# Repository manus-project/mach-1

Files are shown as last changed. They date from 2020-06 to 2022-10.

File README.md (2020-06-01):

# Manus MACH-1

This repository contains designs and assembly instructions for our first generation of manipulator.

 * [Bill of materials](bom.md) - list of materials used
 * [Frame parts](parts) - models of all 3D printer parts
 * [Pritned circuit boards](pcb) - schemes for PCB printing and assembly

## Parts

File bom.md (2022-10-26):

Bill or materials
=================

Manipulator
-----------

| Quantity | Name | Price per piece | Price | Manufacturer | Manufacturer’s code |
|---|---|---|---|---|---|
| 1 | HS-645MG Servo | 28.28 € | 28.28 € | HITEC | |
| 1 | HS-485HB Servo | 16.40 € | 16.40 € | HITEC | |
| 1 | HS-311 Servo | 8.94 € | 8.94 €  | HITEC | |
| 3 | ES08A Servo | 5.50 € | 16.50 € | EMAX | |
| 0.02 | Screw 2.2 mm 6.5 mm, Philips DIN 7982 | 13.08 € | 0.26 €  | TOOLCRAFT | 1068218 |
| 0.032 | Screw 2.2 mm 13 mm, Philips DIN 7982 | 15.54 € | 0.50 €  | TOOLCRAFT | 1068220 |
| 0.01 | PAN Screw TOOLCRAFT, M3, 25mm, DIN 7985 | 2.37 € | 0.02 €  | TOOLCRAFT | 827136 |
| 0.07 | PAN Screw TOOLCRAFT, M3, 20mm, DIN 7985 | 2.95 € | 0.21 €  | TOOLCRAFT | 815411 |
| 0.14 | M3 DIN 934,TOOLCRAFT 131823 | 0.82 € | 0.11 €  | TOOLCRAFT | 131823 |
| 0.24 | 3.2 mm DIN 433, TOOLCRAFT 106698 | 2.78 € | 0.67 €  | TOOLCRAFT | 106698 |
| 1 | SCI 6 A R13-112LP-02 LED GREEN250V/AC 6 A | 3.36 € | 3.36 €  | SCI | 700320 |
| 1 | 5.7 mm 2.1 mm BKL Electronic 072784 | 1.96 € | 1.96 €  | BKL | 72784 |
| 1.1 | Flat cable 10 X 0,14 AWG28 105°C | 0.42 € | 0.46 €  | Neltron | 830-127-10C |
| 1 | Audio cable 2x0,75 black-red | 0.43 € | 0.43 €  | Velleman | LOW2075RB/C |
| 1 | Axial bearing 51111 | 2.82 € | 2.82 €  | Codex | 51111 |

OpenServo board
---------------

| Quantity | PCB tag | Name | Description | Size | Price per piece | Price  | Manufacturer | Manufacturar’s code |
|---|---|---|---|---|---|---|---|---|
| 1 | IC1 | ATMEGA328P-AU |  8 Bit Microcontroller, Low Power High  Performance, ATmega, 20 MHz, 32 KB, 2 KB,  32 Pins, TQFP | TQFP | 3.20 € | 3.20 € | Microchip | ATMEGA328P-AU |
| 11 | C4, C5, C6, C7, C8, C9, C10, C11, C13, C16, C17 | MCB0603R104KCT | smd ceramic capacitor 0.1uF, 16V | V 0603 | 0.01 € | 0.09 € | Multicomp | MCB0603R104KCT |
| 2 | R8, R10 | MC0063W060312K | smd, resistro, 2k, 1% | V 0603 | 0.00 € | 0.01 € | Multicomp | MC0063W060312K |
| 1 | U2 | ZXCT1009F | current sensor, high side | V 0603 | 0.88 € | 0.88 € | Diodes inc. | ZXCT1009F |
| 1 | R2 | MC0063W060311K | smd resistor 1k 1%, 0603 | V 0603 | 0.01 € | 0.01 € | Multicomp | MC0063W060311K |
| 2 | R13, R15 | MC0063W06031100K | smd resistor, 100k 1% | V 0603 | 0.00 € | 0.00 € | Multicomp | MC0063W06031100K |
| 1 | R1 | MCCSM06FTDUR022 | smd current sense resistor, 0.022Ohm +-1% | V 1206 | 0.43 € | 0.43 € | Multicomp | MCCSM06FTDUR022 |
| 2 | U4, U5 | SN74CBT1G125DBVT | logic, switch bus fet sgl | SOT-23-5 | 0.32 € | 0.65 € | Texas Instruments | SN74CBT1G125DBVT |
| 2 | C3, C18 | C1608X7R1C105K080AC | smd ceramic capacitor 1uF, 16V +-10%, X7R | V 0603 | 0.06 € | 0.12 € | TDK | C1608X7R1C105K080AC |
| 4 | C1, C2, C14, C15 | C3216X7R1C106K160AC | smd ceramic capacitor 10uF, 16V +-10%, X7R | V 1206 | 0.30 € | 1.20 € | TDK | C3216X7R1C106K160AC |
| 1 | C12 | MCSH18B102K160CT | smd ceramic capacitor 1000pF, 16V +-10%, X7R | V 0603 | 0.04 € | 0.04 € | Multicomp | MCSH18B102K160CT |
| 1 | U3 | MCP9701AT-E/LT | temperature sensor IC | SC-70, 5pins | 0.39 € | 0.39 € | Microchip | MCP9701AT-E/LT |
| 1 | Q1 | CSTCE20M0V53 | resonator, ceramic, 20MHz, smd | | 0.43 € | 0.43 € | MURATA | CSTCE20M0V53-R0 |
| 1 | L1 | MLF1608E100K | inductor, high frequency, 10uH +-10 | V 0603 | 0.21 € | 0.21 € | TDK | MLF1608E100K |
| 2 | Q2, Q3 | IRF7317PBF | dual MOSFET, N and P channel, 6.6A, 20V | SOIC | 0.84 € | 1.67 € | INFINEON | IRF7317PBF |
| 2 | Q4, Q5 | NX7002BK | N Channel, 270 mA, 60 V, 2.2 ohm, 10 V, 1.6 V | SOT-23 | 0.04 € | 0.08 € | NEXPERIA | NX7002BKR |
| 7 | R4. R5, R7, R16, R17, R18, R19 | MC0063W0603110K | 10k 1% | V 0603 | 0.00 € | 0.03 € | Multicomp | MC0063W0603110K |
| 4 | R9, R11, R12, R14 | MC0063W0603110R | 10 R 1% | V 0603 | 0.00 € | 0.01 € | Multicomp | MC0063W0603110R |
| 1 | R3 | MC0063W060317K5 | 7.5k 1% | V 0603 | 0.00 € | 0.00 € | Multicomp | MC0063W060317K5 |
| 0.125 | | Header, male | 2x40 | | 0.34 € | 0.04 € | Neltron | 2213S-80G |
| 1 | | Connector | conector speedy 6 fimale | | 0.27 € | 0.27 € | Amphenol | T812106A101CEU |
| 1 | | PCB | | | 2.10 € | 2.10 € | | |

Raspberry Pi Shield
-------------------

| Quantity | PCB tag | Name | Price per piece | Price  | Manufacturer | manufacturer’s code |
|---|---|---|---|---|---|---|
| 1 | D1 | LITTELFUSE  SMBJ5.0A  TVS Diode, Transil SMBJ Series, Unidirectional, 5 V, 9.2 V, DO-214AA, 2 Pins | 0.32 € | 0.32 € | LITTELFUSE | SMBJ5.0A |
| 1 | IC1 | ON SEMICONDUCTOR  PCA9306DTR2G  Voltage Level Translator, Bidirectional, 2 Input, 64 mA, 1.5 ns, 0 V to 5.5 V, TSSOP-8 | 0.72 € | 0.72 € | ON SEMICONDUCTOR | PCA9306DTR2G |
| 1 | U1 | TEXAS INSTRUMENTS  LM4670SD  Audio Power Amplifier, D, 1 Channel, 3 W, 2.4V to 5.5V, LLP, 8 Pins | 1.02 € | 1.02 € | TEXAS INSTRUMENTS | LM4670SD |
| 2 | C2, C9 | PANASONIC ELECTRONIC COMPONENTS  EEEFPJ470UAR  SMD Aluminium Electrolytic Capacitor, Radial Can - SMD, 47 µF, 6.3 V, 0.85 ohm, FP Series | 0.32 € | 0.64 € | PANASONIC ELECTRONIC COMPONENTS | EEEFPJ470UAR |
| 6 | C3, C4, C5, C6, C8, C11 | KEMET  C0805C104K4RACTU  SMD Multilayer Ceramic Capacitor, 0805 [2012 Metric], 0.1 µF, 16 V, ± 10%, X7R, C Series | 0.06 € | 0.37 € | KEMET | C0805C104K4RACTU |
| 3 | C1, C7, C10 | KEMET  C0805C105K4RACTU  SMD Multilayer Ceramic Capacitor, 0805 [2012 Metric], 1 µF, 16 V, ± 10%, X7R, C Series | 0.07 € | 0.20 € | KEMET | C0805C105K4RACTU |
| 1 | U$1 | BOURNS  MF-MSMF150-2  PPTC Resettable Fuse, SMD, MF-MSMF Series, 1.5 A, 3 A, 6 V, -40 °C | 0.32 € | 0.32 € | BOURNS | MF-MSMF150-2 |
| 1 | | PRO SIGNAL  ABS-215-RC  Speaker, Mini, Mylar Cone, 1.5 W, 8 ohm, 550 Hz to 4500 Hz | 2.07 € | 2.07 € | PRO SIGNAL | ABS-215-RC |
| 1 | Q1 | VISHAY  SI4477DY-T1-GE3  MOSFET Transistor, P Channel, -26.6 A, -20 V, 0.0051 ohm, -4.5 V, -1.5 V | 1.30 € | 1.30 € | VISHAY | SI4477DY-T1-GE3 |
| 1 | Q2 | FAIRCHILD SEMICONDUCTOR  2N7002  MOSFET Transistor, N Channel, 115 mA, 60 V, 1.2 ohm, 10 V, 2.1 V | 0.19 € | 0.19 € | FAIRCHILD SEMICONDUCTOR |  2N7002 |
| 1 | IC2 | ON SEMICONDUCTOR  MC14027BDG  Flip-Flop, Master/Slave,Complementary Output, Positive Edge, MC14027, JK, 150 ns, 13 MHz, 8.8 mA | 0.42 € | 0.42 € | ON SEMICONDUCTOR | MC14027BDG |
| 1 | SV1 | LETVICA 2x6 Ž PROF. VISOKA R=2,54 | 0.46 € | 0.46 € | Neltron | 6803S-12-80 |
| 4 | 5V, SPEAKER, P_M, M | VRSTNA SPONKA ZA TIV 90° 2P - NIZKA (ZELENA) | 0.35 € | 1.40 € | TE Connectivity | 0-0282836-2 |
| 2 | R12, R15 | Resistor 10R 0603 1% SMD | 0.03 € | 0.05 € | Vishay | CRCW060310R0FKTABC  |
| 2 | R3, R4 | Resistor 340R 0603 1% SMD | 0.03 € | 0.05 € | Yageo | RC0603FR-07340RL |
| 3 | R17, R18, R19 | Resistor 511R 0603 1% SMD | 0.03 € | 0.08 € | Yageo | RC0603FR-07511RL |
| 3 | R16 | Resistor 1K 0603 1% SMD | 0.03 € | 0.08 € | Vishay | CRCW06031K00FKTABC  |
| 1 | R21 | Resistor 2K 0603 1% SMD 7" | 0.03 € | 0.03 € | Vishay | CRCW06032K00FKTABC  |
| 3 | R13, R14, R20 | Resistor 10K 0603 1% SMD | 0.03 € | 0.08 € | Vishay | CRCW060310K0FKTABC  |
| 6 | R5, R6, R7, R8, R9, R10 | Resistor 150K 0603 1% SMD | 0.03 € | 0.15 € | Vishay | CRCW0603150KFKTABC  |
| 0.125 | SV2 | Header2X40 M R=2,54 | 0.34 € | 0.04 € | Neltron | 2213S-80G |
| 1 | | PCB | 4.38 € | 4.38 € | | |

Other
-----

| Quantity | Name | Price per piece | Price | Manufacturer | Manufacturer’s code |
|---|---|---|---|---|---|
| 1 | RASPBERRYPI3-MODB-1GB | 32.79 € | 32.79 € | RASPBERRY-PI | RASPBERRYPI3-MODB-1GB |
| 1 | SanDisk SDHC 16GB Ultra UHS-I 80MB/s | 7.41 € | 7.41 €  | SanDisk | |
| 1 | Mean Well SGA60E05-P1J 5 V/DC 6000 mA 30 W | 30.29 € | 30.29 € | Mean Well | SGA60E05-P1J |
| 0.3 | Filament PrimaValue PLA 1kg | 22.13 € | 6.64 €  | PRIMA | |

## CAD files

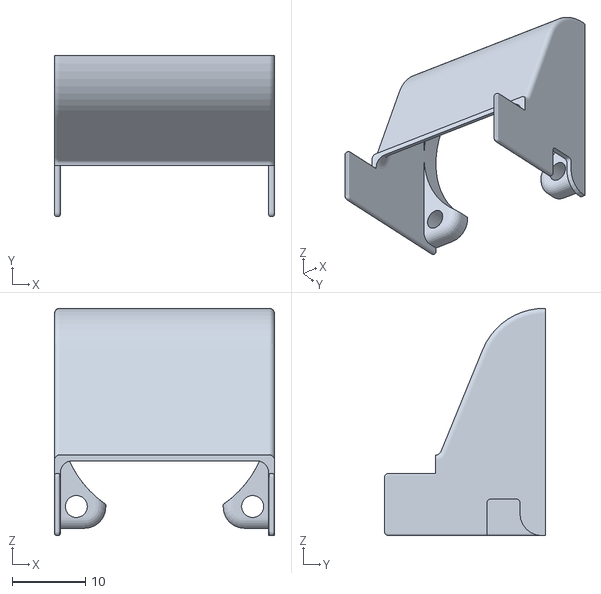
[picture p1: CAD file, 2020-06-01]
parts/base/cooling_tunnel.obj
30.0 x 22.0 x 31.0

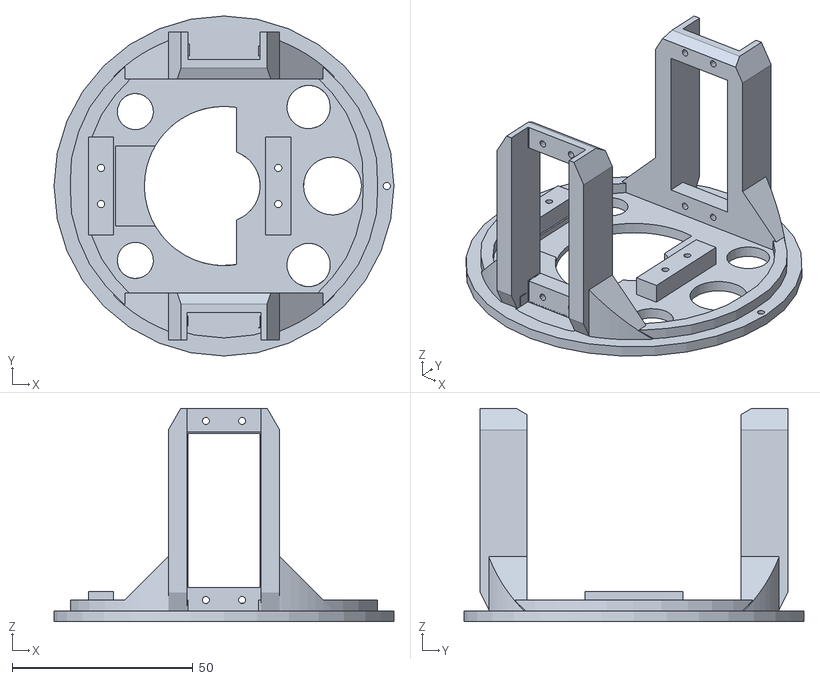
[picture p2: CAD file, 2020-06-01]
parts/manipulator/base_A.obj
94.0 x 94.0 x 59.0

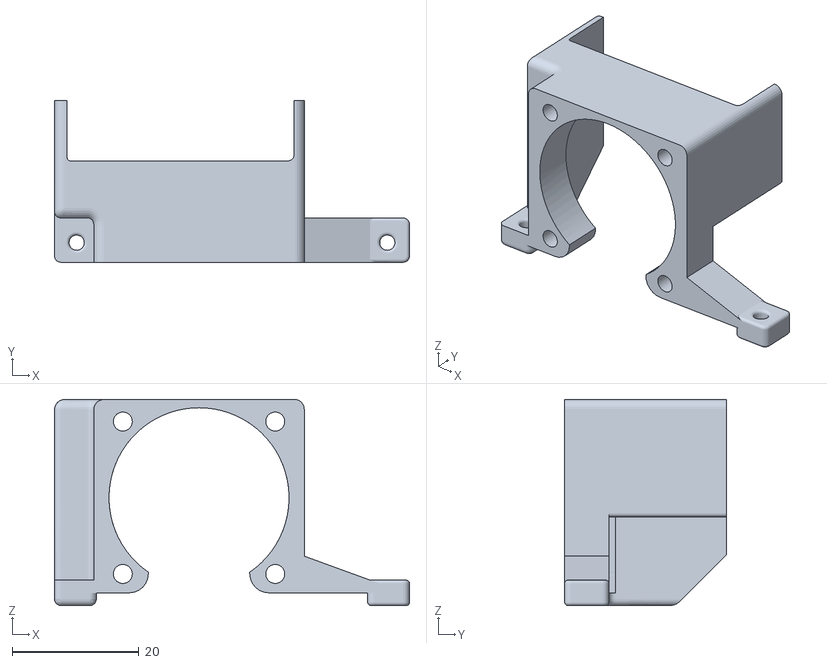
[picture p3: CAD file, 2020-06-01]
parts/base/cooling_fan.obj
56.0 x 25.5 x 32.5

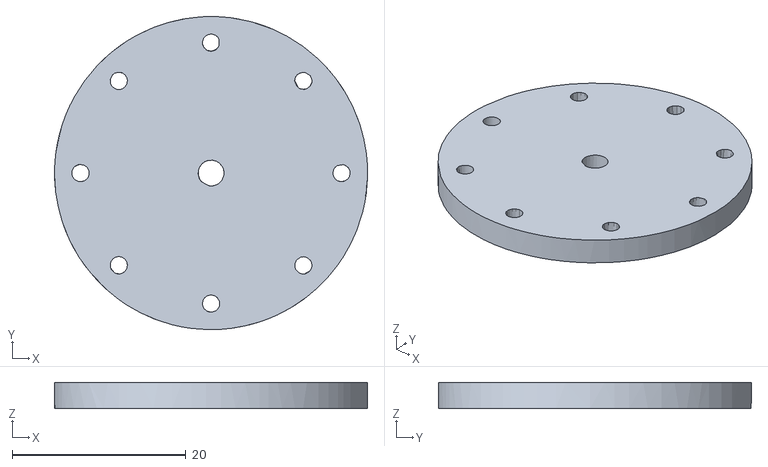
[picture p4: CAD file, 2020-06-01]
parts/manipulator/base_O.obj
36.0 x 36.0 x 3.00

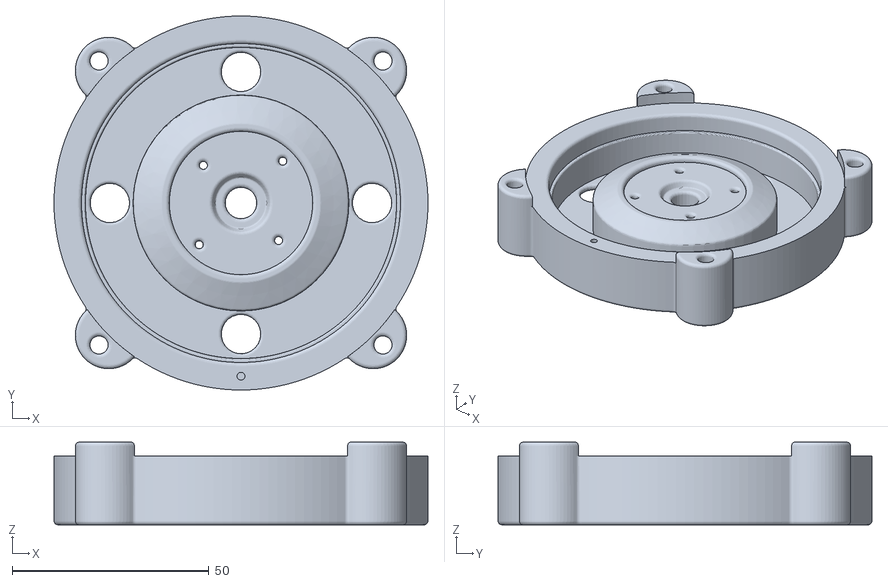
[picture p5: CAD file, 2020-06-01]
parts/base/base.obj
95.0 x 95.0 x 21.0

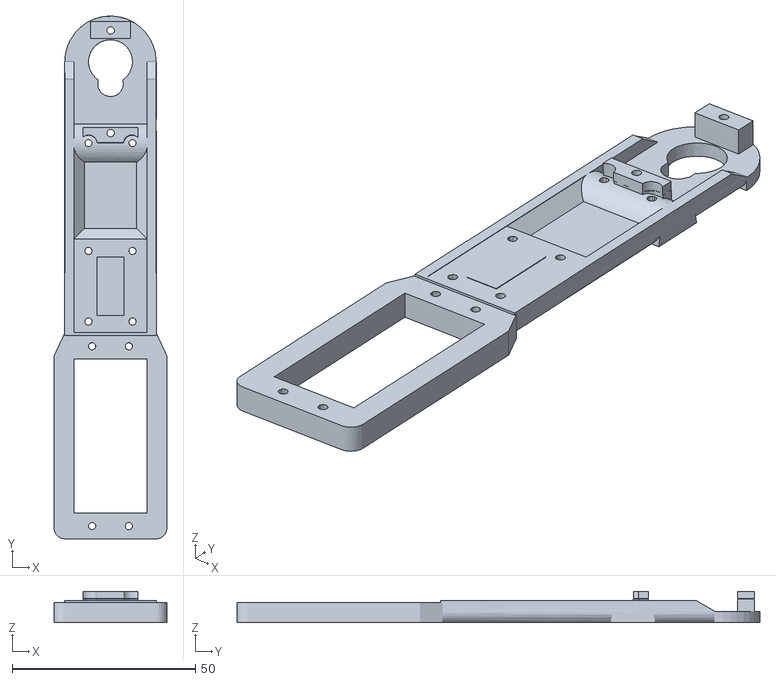
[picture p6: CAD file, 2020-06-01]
parts/manipulator/joint2_I_p1.obj
30.8 x 142.5 x 8.50

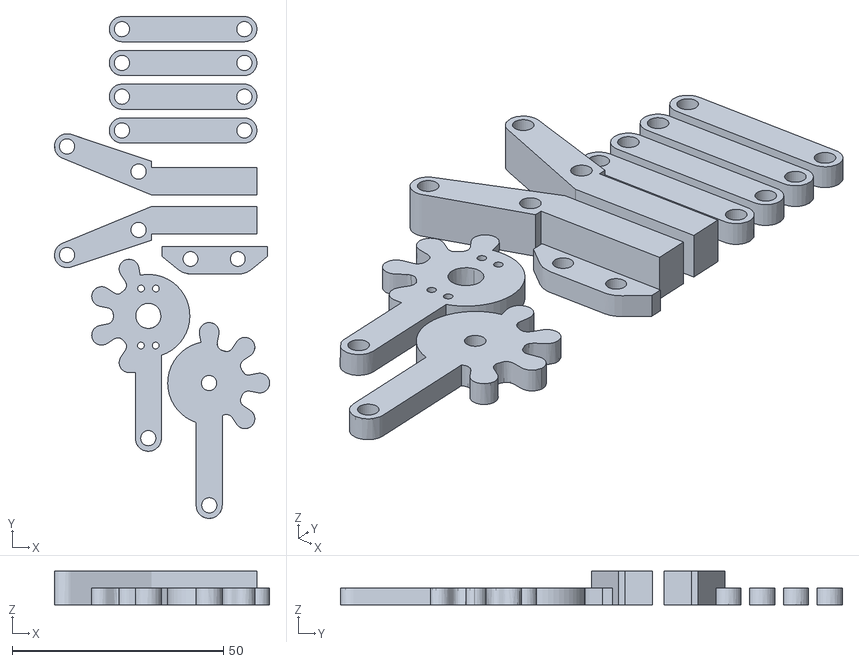
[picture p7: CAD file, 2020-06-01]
parts/manipulator/gripper.obj
51.0 x 118.9 x 8.00

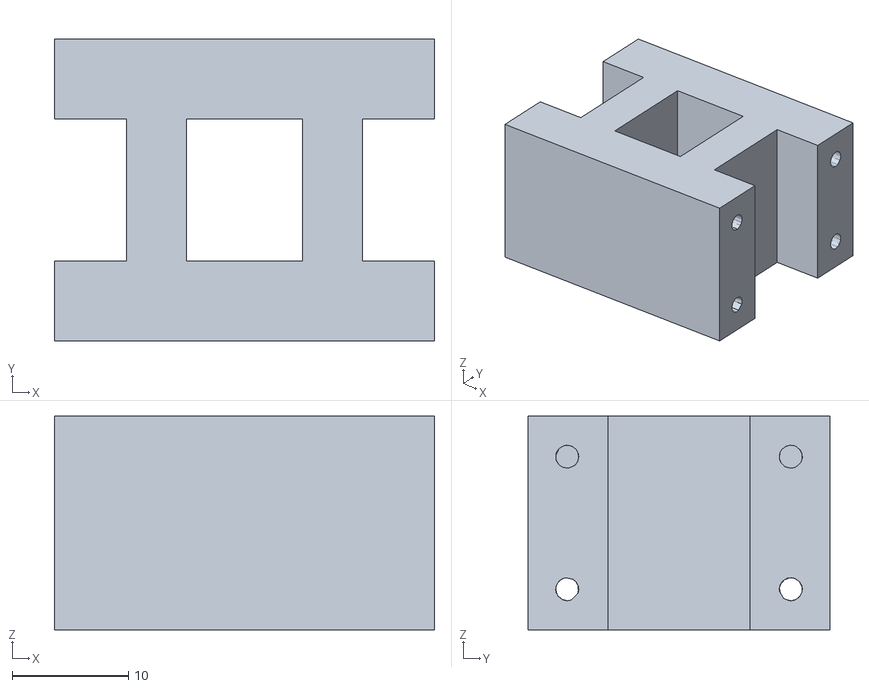
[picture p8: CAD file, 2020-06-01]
parts/manipulator/joint2_H.obj
32.7 x 26.0 x 18.4

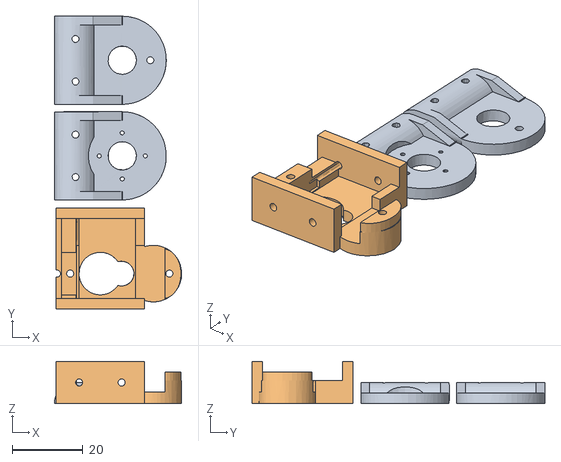
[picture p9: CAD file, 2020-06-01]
parts/manipulator/joint3.obj
36.0 x 82.7 x 12.0

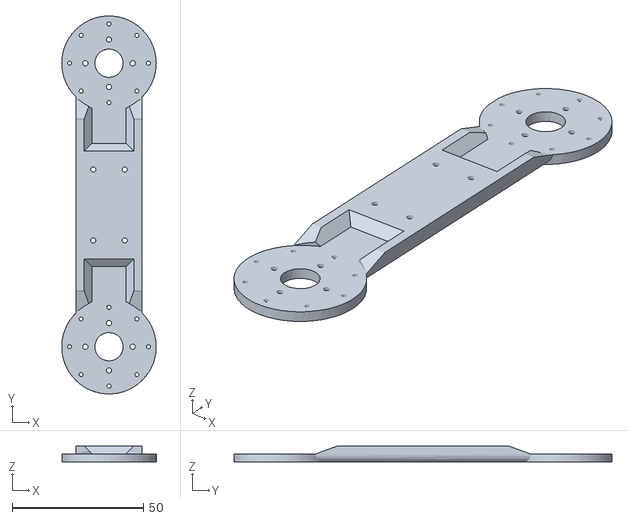
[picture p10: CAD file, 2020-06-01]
parts/manipulator/joint1_I.obj
36.0 x 144.0 x 6.00

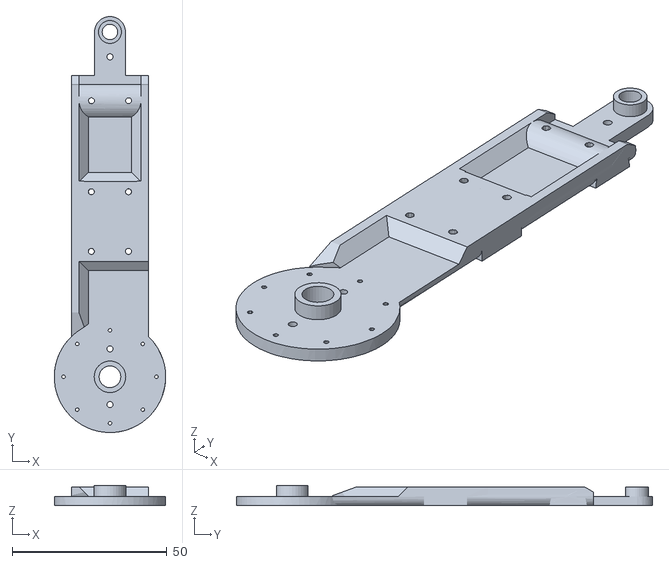
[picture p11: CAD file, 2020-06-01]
parts/manipulator/joint2_I_p2.obj
36.0 x 134.3 x 6.50

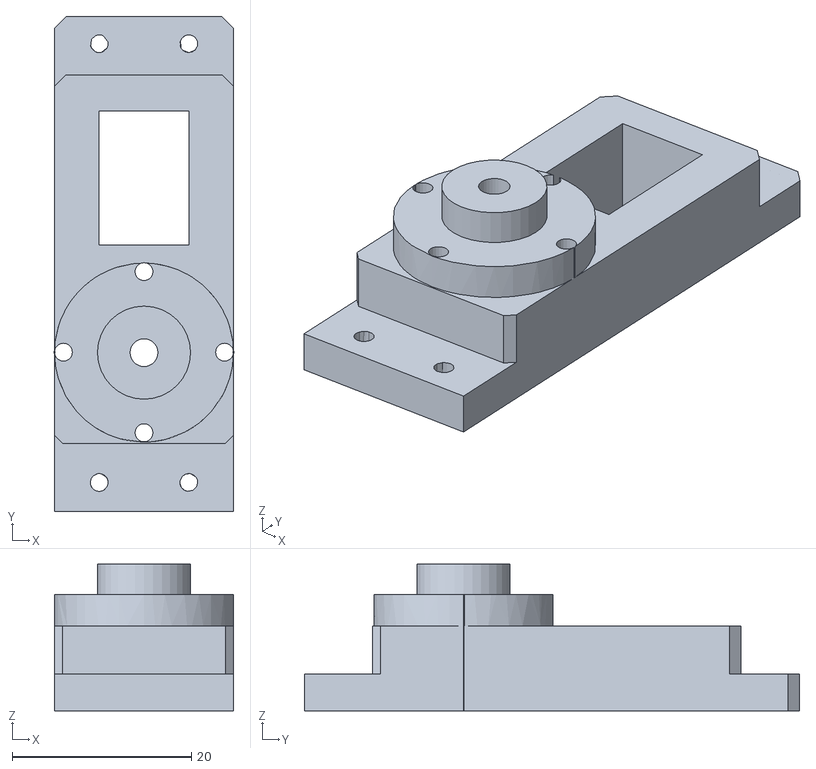
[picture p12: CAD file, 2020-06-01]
parts/manipulator/base_Servo.obj
20.0 x 55.3 x 16.4

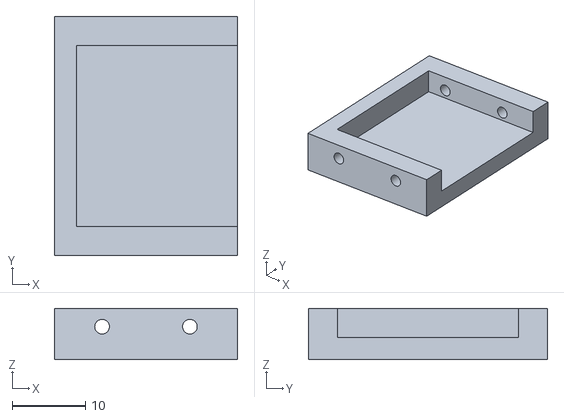
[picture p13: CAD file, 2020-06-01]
parts/manipulator/joint2_L.obj
25.0 x 32.7 x 7.00

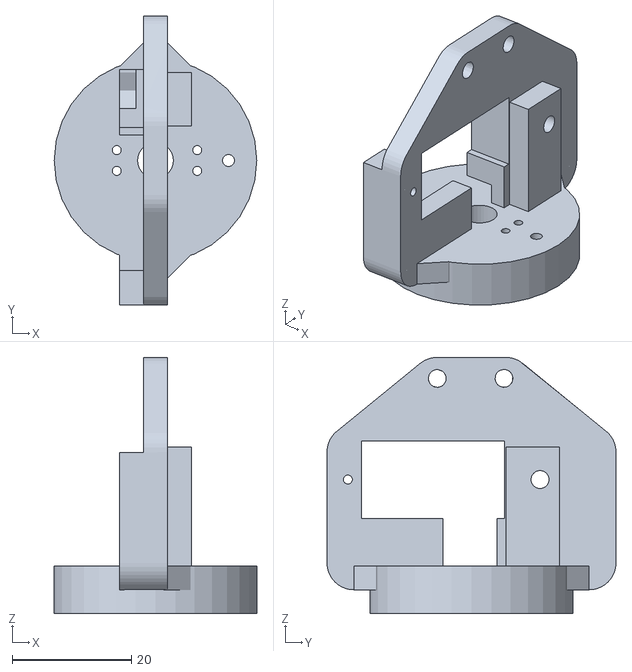
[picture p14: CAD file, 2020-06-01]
parts/manipulator/joint4.obj
34.0 x 48.5 x 43.0

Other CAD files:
parts/manipulator/joint1_H.obj

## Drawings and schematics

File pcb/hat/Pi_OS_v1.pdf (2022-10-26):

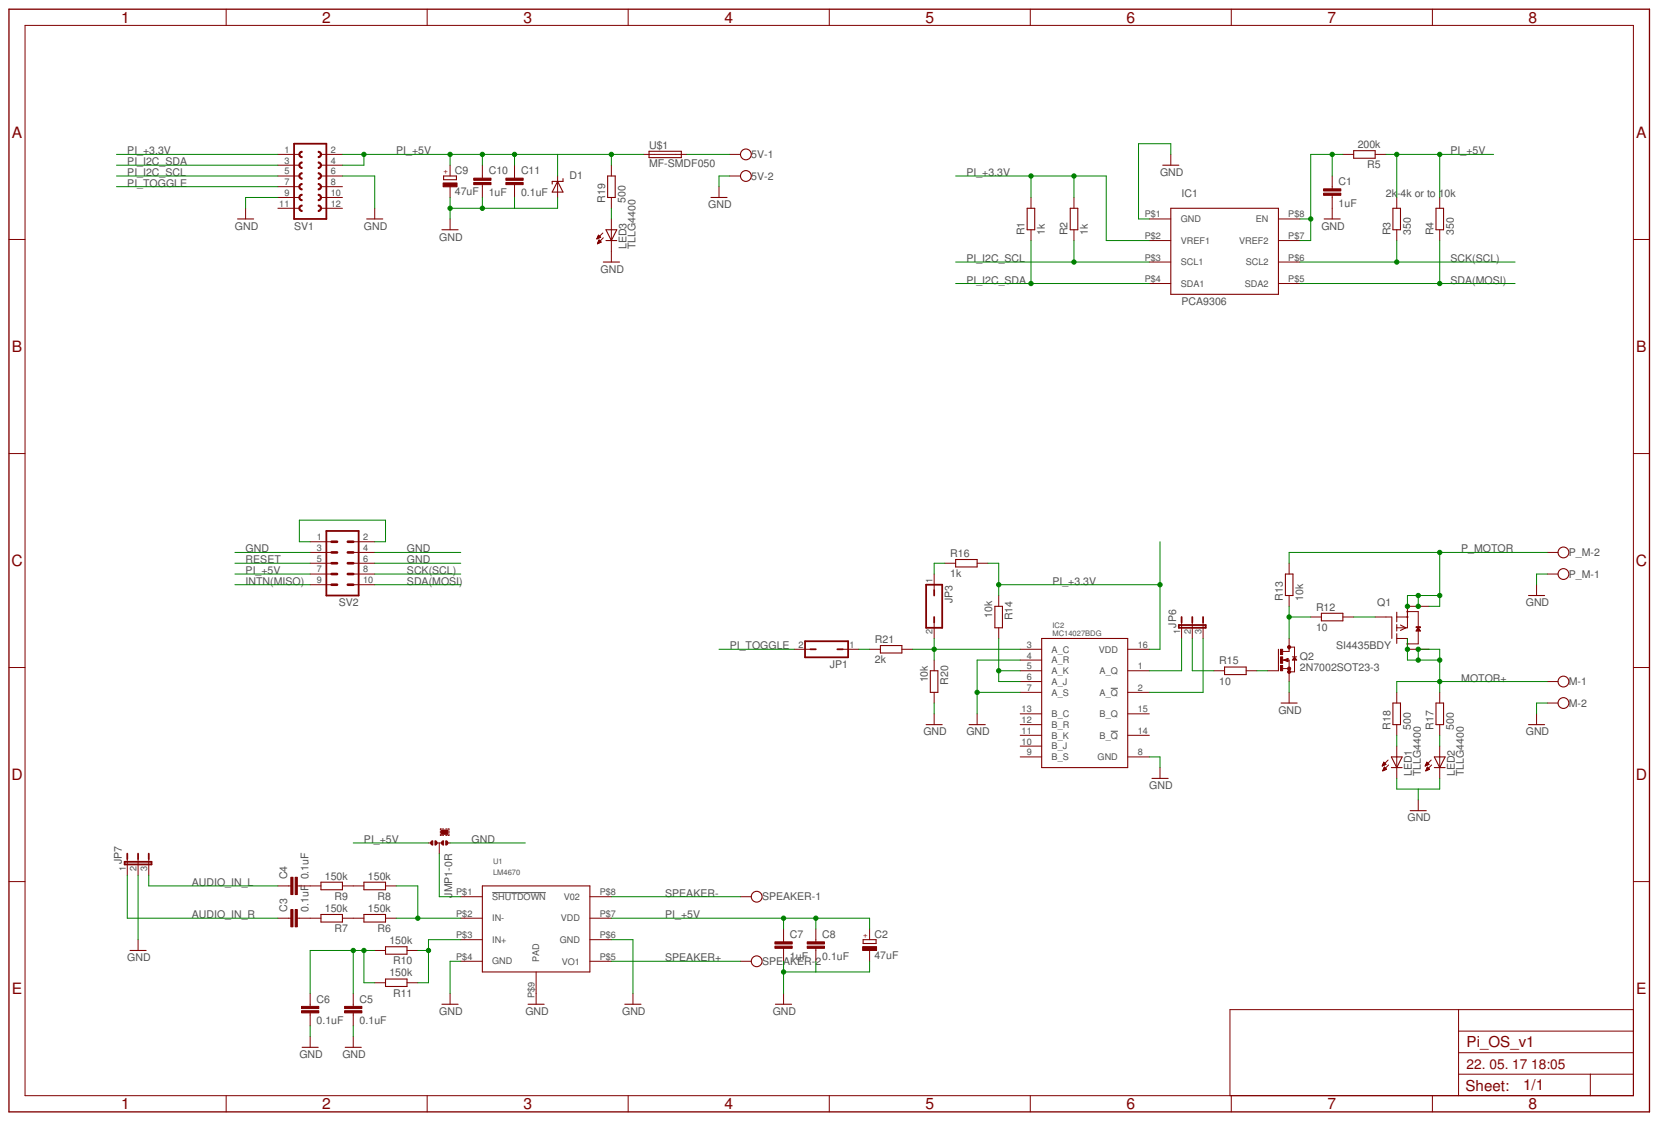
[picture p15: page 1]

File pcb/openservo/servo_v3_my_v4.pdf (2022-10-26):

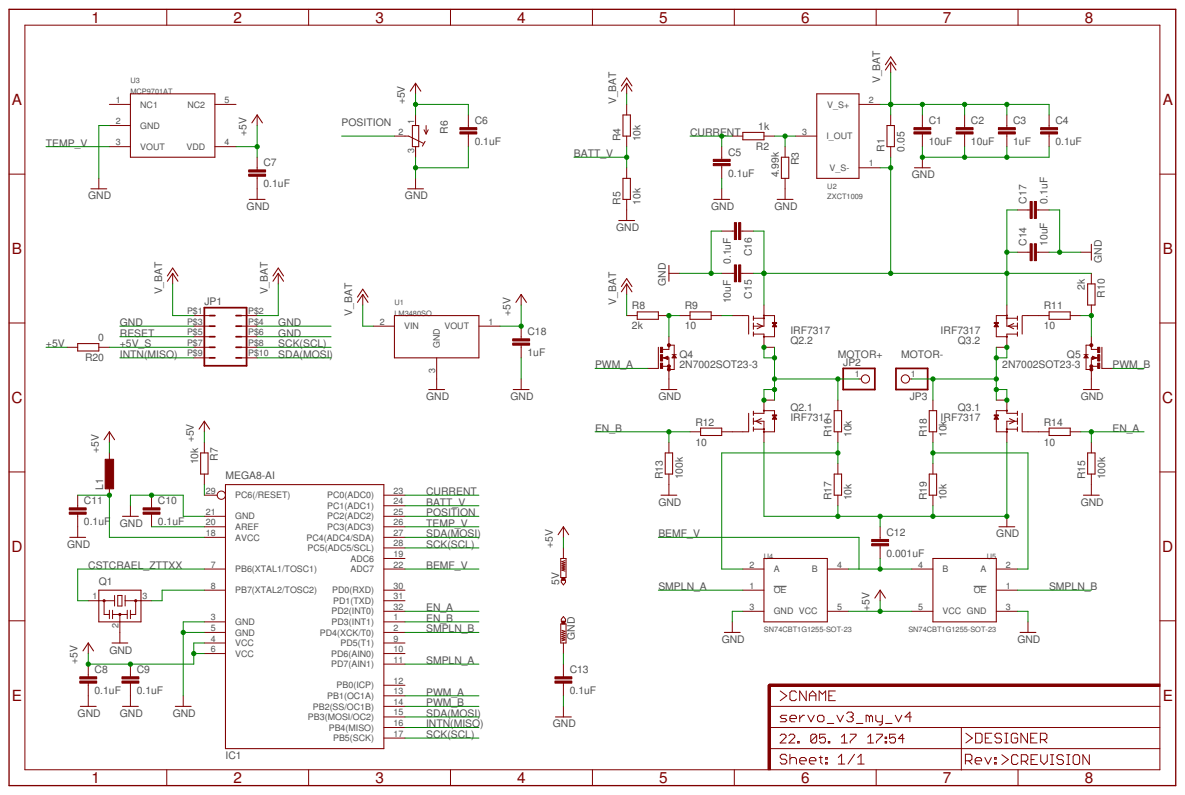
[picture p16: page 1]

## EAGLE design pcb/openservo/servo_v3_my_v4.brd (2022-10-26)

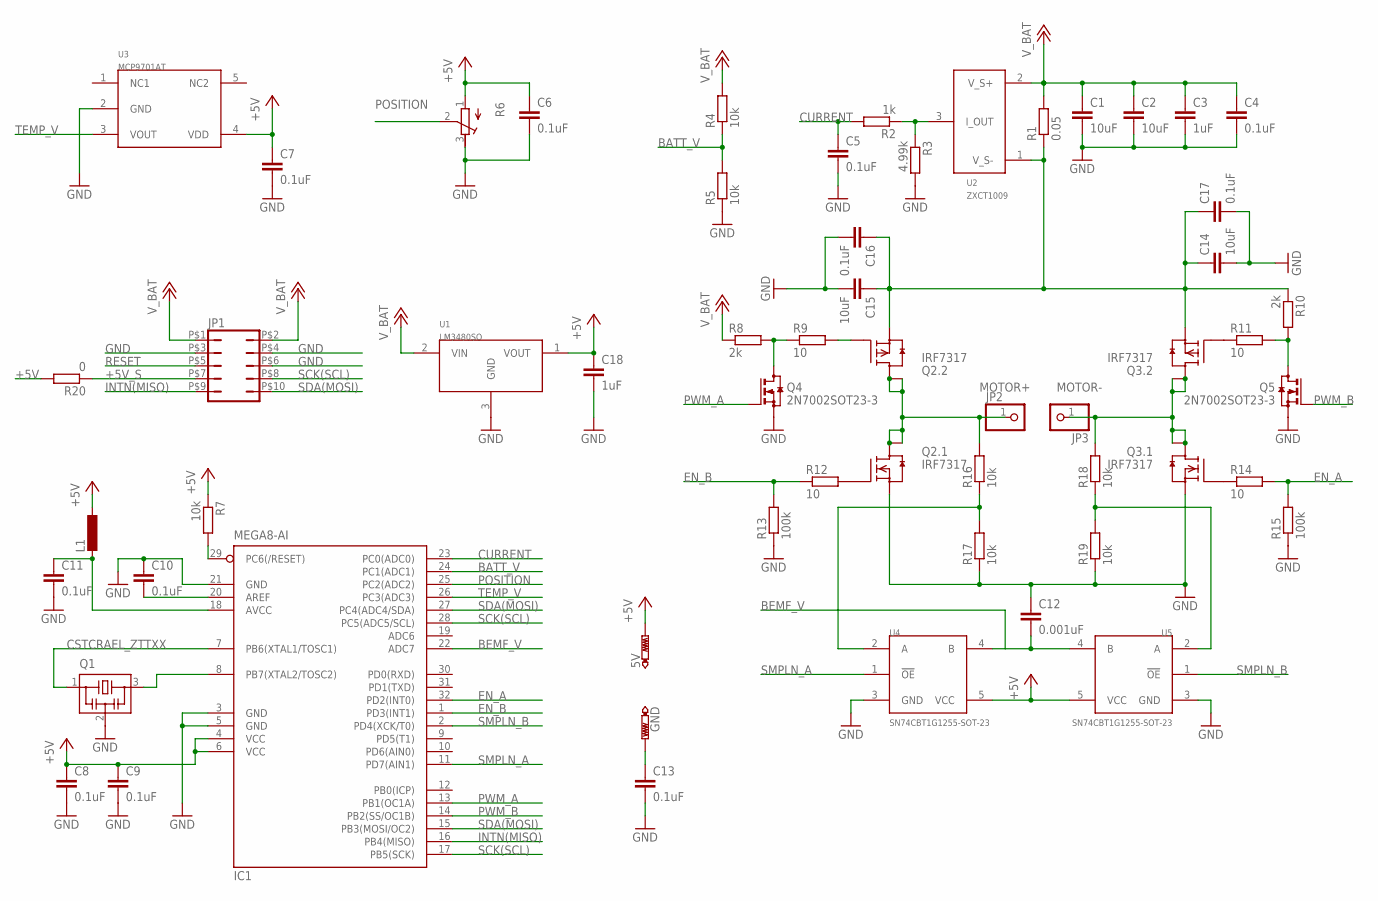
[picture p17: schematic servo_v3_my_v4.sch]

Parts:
5V: PTR1B1,27; B1,27
C1, C2, C14, C15: 10uF; C1206
C3, C18: 1uF; C0603
C4, C5, C6, C7, C8, C9, C10, C11, C13, C16, C17: 0.1uF; C0603
C12: 0.001uF; C0603; MPN BFC237052102
GND: PTR1B1,27; B1,27
IC1: MEGA8-AI; TQFP32-08
JP1: JP5QJP5Q_SMD; JP5_DUAL_SIDE
JP2, JP3: PINHD-1X1; 1X01
L1: L-EUL0603; C0603
Q1: CSTCRAEL_ZTTXX; CSTCE_WIDE
Q2, Q3: IRF7317; SO-8
Q4, Q5: 2N7002SOT23-3; SOT23
R1: 0.05; R1206
R2: 1k; R0603
R3: 4.99k; R0603
R4, R5, R7, R16, R17, R18, R19: 10k; R0603
R6: R-TRIMM; RTRIM_SMALL
R8, R10: 2k; R0603
R9, R11, R12, R14: 10; R0603
R13, R15: 100k; R0603
R20: 0; R0603
U1: LM3480SO; SOT23
U2: ZXCT1009; SOT23
U3: MCP9701AT; SC-70-5
U4, U5: SN74CBT1G1255-SOT-23; SOT23-5

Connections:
+5V: 5V.TP, C6.1, C7.1, C8.1, C9.1, C18.1, IC1.4 (VCC), IC1.6 (VCC), L1.1, R6.1 (A), R7.1, R20.2, U1.1 (VOUT), U3.4 (VDD), U4.5 (VCC), U5.5 (VCC)
+5V_S: JP1.P$7 (7), R20.1
BATT_V: IC1.24 (PC1(ADC1)), R4.1, R5.2
BEMF_V: C12.2, IC1.22 (ADC7), U4.4 (B), U5.4 (B)
CURRENT: C5.1, IC1.23 (PC0(ADC0)), R2.2
EN_A: IC1.32 (PD2(INT0)), R14.2, R15.2
EN_B: IC1.1 (PD3(INT1)), R12.1, R13.2
GND: C1.2, C2.2, C3.2, C4.2, C5.2, C6.2, C7.2, C8.2, C9.2, C10.1, C11.2, C12.1, C13.2, C14.2, C15.2, C16.2, C17.2, C18.2, IC1.3 (GND), IC1.5 (GND), IC1.21 (GND), JP1.P$3 (3), JP1.P$4 (4), JP1.P$6 (6), Q1.2, Q2.1 (S), Q3.1 (S), Q4.2 (S), Q5.2 (S), R3.2, R5.1, R6.3 (E), R13.1, R15.1, R17.1, R19.1, U1.3 (GND), U3.2 (GND), U4.3 (GND), U5.3 (GND)
INTN(MISO): IC1.16 (PB4(MISO)), JP1.P$9 (9)
MOTOR+: JP2.1, Q2.5 (D), Q2.6 (D), Q2.7 (D), Q2.8 (D), R16.2
MOTOR-: JP3.1, Q3.5 (D), Q3.6 (D), Q3.7 (D), Q3.8 (D), R18.2
unnamed: R2.1, R3.1, U2.3 (I_OUT)
unnamed: IC1.7 (PB6(XTAL1/TOSC1)), Q1.1
unnamed: IC1.8 (PB7(XTAL2/TOSC2)), Q1.3
unnamed: C11.1, IC1.18 (AVCC), L1.2
unnamed: C10.2, IC1.20 (AREF)
unnamed: C14.1, C15.1, C16.1, C17.1, Q2.3 (S), Q3.3 (S), R1.1, R10.1, U2.1 (V_S-)
unnamed: Q4.3 (D), R8.2, R9.1
unnamed: Q2.4 (G), R9.2
unnamed: Q5.3 (D), R10.2, R11.2
unnamed: C13.1, GND.TP
unnamed: Q2.2 (G), R12.2
unnamed: Q3.2 (G), R14.1
unnamed: Q3.4 (G), R11.1
unnamed: R18.1, R19.2, U5.2 (A)
unnamed: R16.1, R17.2, U4.2 (A)
POSITION: IC1.25 (PC2(ADC2)), R6.2 (S)
PWM_A: IC1.13 (PB1(OC1A)), Q4.1 (G)
PWM_B: IC1.14 (PB2(SS/OC1B)), Q5.1 (G)
RESET: IC1.29 (PC6(/RESET)), JP1.P$5 (5), R7.2
SCK(SCL): IC1.17 (PB5(SCK)), IC1.28 (PC5(ADC5/SCL)), JP1.P$8 (8)
SDA(MOSI): IC1.15 (PB3(MOSI/OC2)), IC1.27 (PC4(ADC4/SDA)), JP1.P$10 (10)
SMPLN_A: IC1.11 (PD7(AIN1)), U4.1 (!OE)
SMPLN_B: IC1.2 (PD4(XCK/T0)), U5.1 (!OE)
TEMP_V: IC1.26 (PC3(ADC3)), U3.3 (VOUT)
V_BAT: C1.1, C2.1, C3.1, C4.1, JP1.P$1 (1), JP1.P$2 (2), R1.2, R4.2, R8.1, U1.2 (VIN), U2.2 (V_S+)

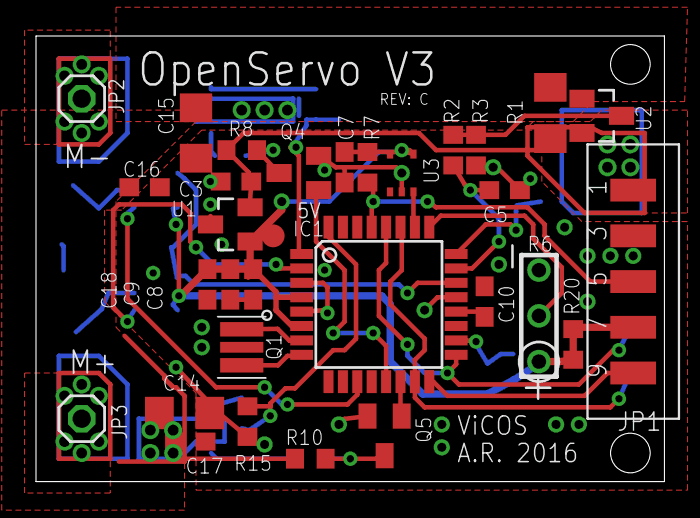
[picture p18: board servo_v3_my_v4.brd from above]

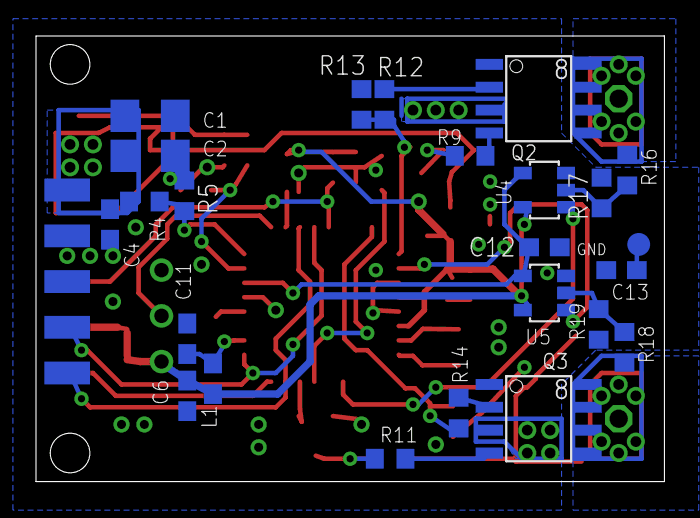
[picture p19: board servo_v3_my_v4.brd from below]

Board: 2 copper layers, 34.9 x 24.8 mm, 55 parts (24 on the bottom side), 36 nets.

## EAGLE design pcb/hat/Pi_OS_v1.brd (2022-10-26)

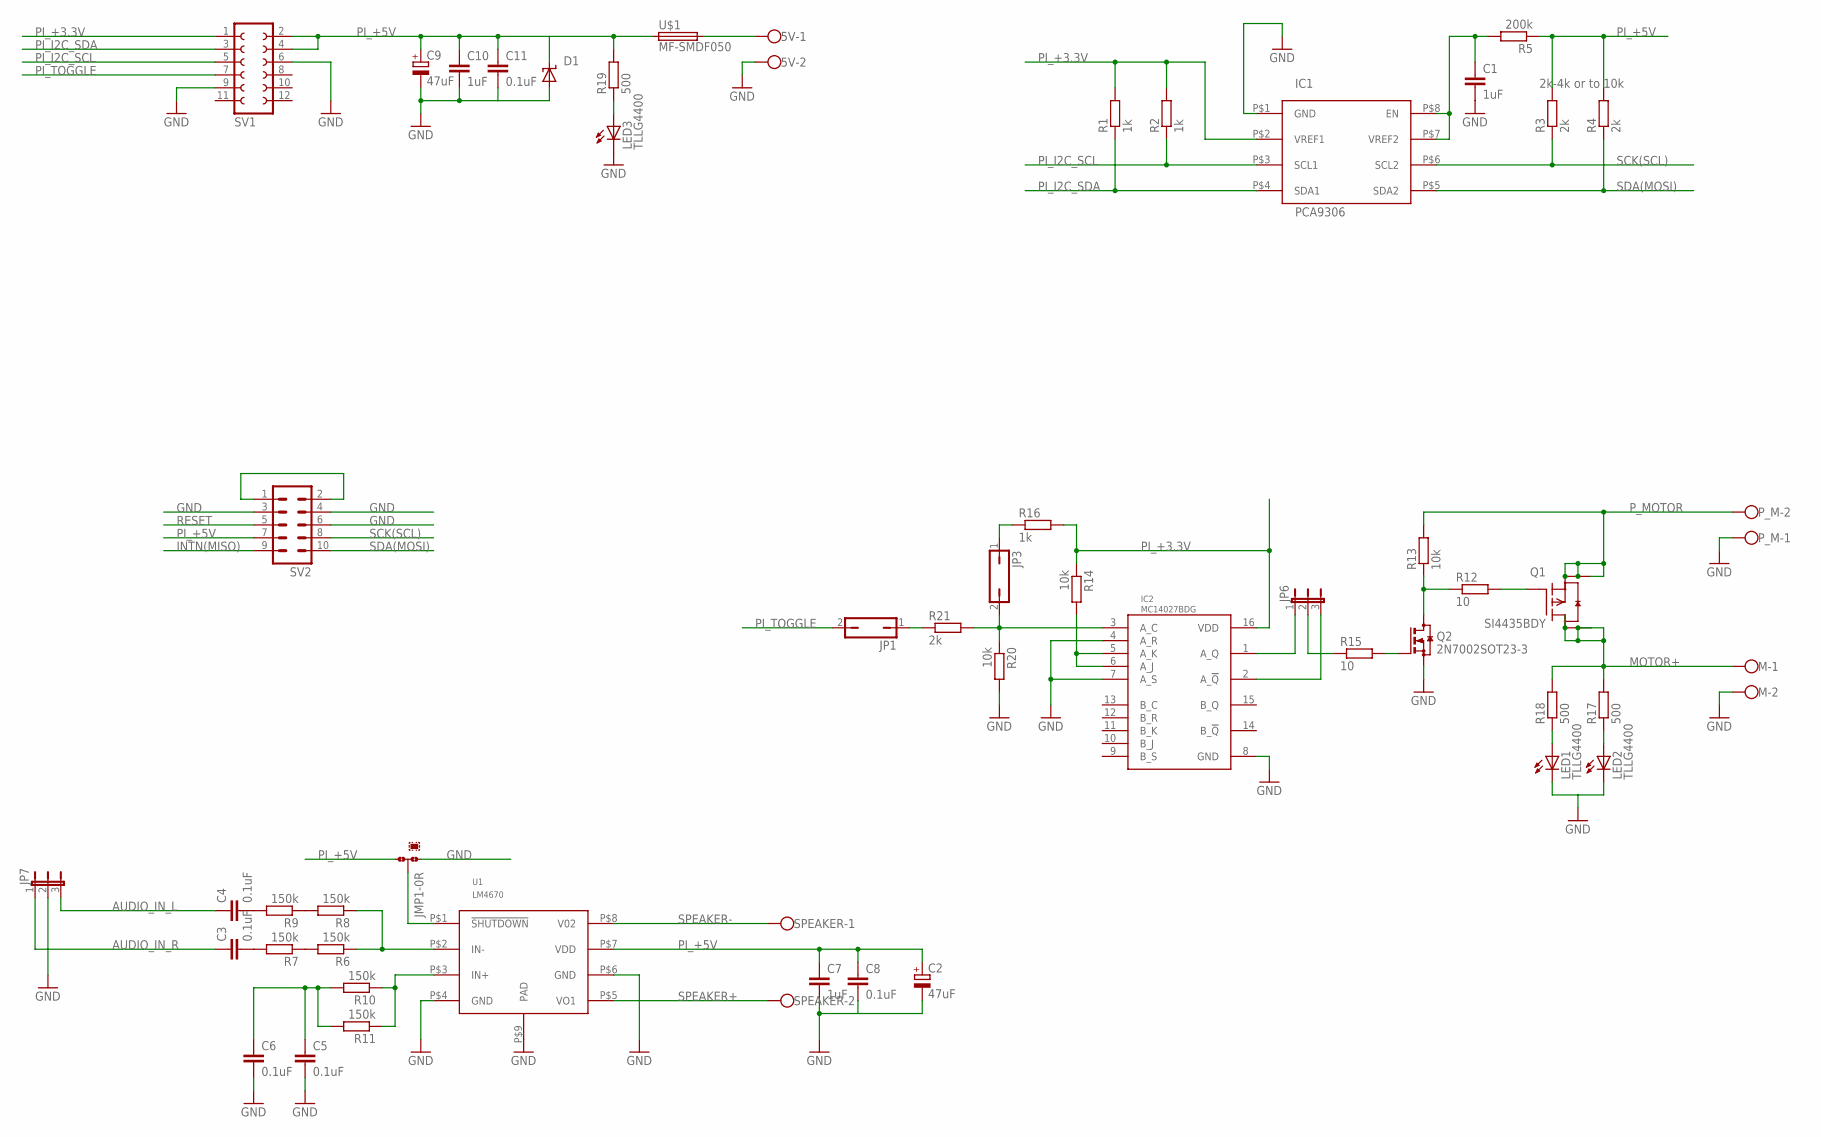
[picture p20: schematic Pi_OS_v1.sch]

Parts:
5V: W237-102
C1, C7, C10: 1uF; C1206
C2, C9: 47uF; 153CLV-0505
C3, C4, C5, C6, C8, C11: 0.1uF; C1206
D1: SUPPRESSOR-SMBJ; SMBJ
IC1: PCA9306; TSSOP8
IC2: MC14027BDG; SOIC16
JMP1: 0R-JUMPB; B0R-JMP
JP1, JP3: JP1Q; JP1
JP6, JP7: JP2E; JP2
LED1, LED2, LED3: TLLG4400; LED3MM
M: W237-102
P_M: W237-102
Q1: SI4435BDY; SOIC8
Q2: 2N7002SOT23-3; SOT23
R1, R2, R16: 1k; R0603
R3, R4, R21: 2k; R0603
R5: 200k; R0603
R6, R7, R8, R9, R10, R11: 150k; R0603
R12, R15: 10; R0603
R13, R14, R20: 10k; R0603
R17, R18, R19: 500; R0603
SPEAKER: W237-102
SV1: FE06-2
SV2: MA05-2
U1: LM4670; MSOP-08P
U$1: MF-SMDF050

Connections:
AUDIO_IN_L: C4.1, JP7.3
AUDIO_IN_R: C3.1, JP7.1
GND: 5V.2, C1.2, C2.-, C5.2, C6.2, C7.2, C8.2, C9.-, C10.2, C11.2, D1.A, IC1.P$1 (GND), IC2.4 (A_R), IC2.7 (A_S), IC2.8 (GND), JMP1.1, JP7.2, LED1.K (C), LED2.K (C), LED3.K (C), M.2, P_M.1, Q2.2 (S), R20.2, SV1.6, SV1.9, SV2.3, SV2.4, SV2.6, U1.P$4 (GND), U1.P$6 (GND), U1.P$9 (PAD)
INTN(MISO): SV2.9
MOTOR+: M.1, Q1.5 (D), Q1.6 (D), Q1.7 (D), Q1.8 (D), R17.2, R18.2
unnamed: JP6.2, R15.1
unnamed: IC2.1 (A_Q), JP6.1
unnamed: IC2.2 (A_!Q), JP6.3
unnamed: 5V.1, U$1.2
unnamed: C1.1, IC1.P$7 (VREF2), IC1.P$8 (EN), R5.2
unnamed: IC2.5 (A_K), IC2.6 (A_J), R14.2
unnamed: IC2.3 (A_C), JP3.2, R20.1, R21.2
unnamed: SV2.1, SV2.2
unnamed: R6.1, R8.1, U1.P$2 (IN-)
unnamed: R10.1, R11.1, U1.P$3 (IN+)
unnamed: R6.2, R7.1
unnamed: R8.2, R9.1
unnamed: C3.2, R7.2
unnamed: C4.2, R9.2
unnamed: C5.1, C6.1, R10.2, R11.2
unnamed: Q2.3 (D), R12.1, R13.1
unnamed: Q1.4 (G), R12.2
unnamed: Q2.1 (G), R15.2
unnamed: JP3.1, R16.1
unnamed: JP1.1, R21.1
unnamed: JMP1.2, U1.P$1 (!SHUTDOWN)
unnamed: LED2.A, R17.1
unnamed: LED1.A, R18.1
unnamed: LED3.A, R19.1
PI_+3.3V: IC1.P$2 (VREF1), IC2.16 (VDD), R1.2, R2.2, R14.1, R16.2, SV1.1
PI_+5V: C2.+, C7.1, C8.1, C9.+, C10.1, C11.1, D1.C, JMP1.3, R3.2, R4.2, R5.1, R19.2, SV1.2, SV1.4, SV2.7, U1.P$7 (VDD), U$1.1
PI_I2C_SCL: IC1.P$3 (SCL1), R2.1, SV1.5
PI_I2C_SDA: IC1.P$4 (SDA1), R1.1, SV1.3
PI_TOGGLE: JP1.2, SV1.7
P_MOTOR: P_M.2, Q1.1 (S), Q1.2 (S), Q1.3 (S), R13.2
RESET: SV2.5
SCK(SCL): IC1.P$6 (SCL2), R3.1, SV2.8
SDA(MOSI): IC1.P$5 (SDA2), R4.1, SV2.10
SPEAKER+: SPEAKER.2, U1.P$5 (VO1)
SPEAKER-: SPEAKER.1, U1.P$8 (V02)

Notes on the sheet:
2k-4k or to 10k

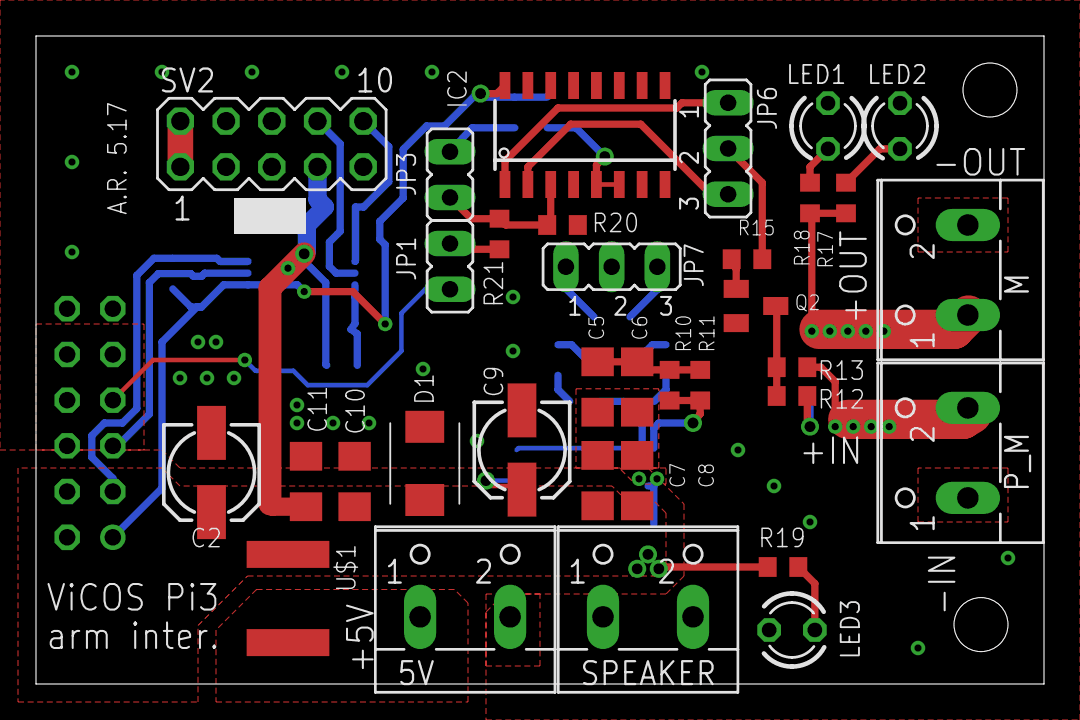
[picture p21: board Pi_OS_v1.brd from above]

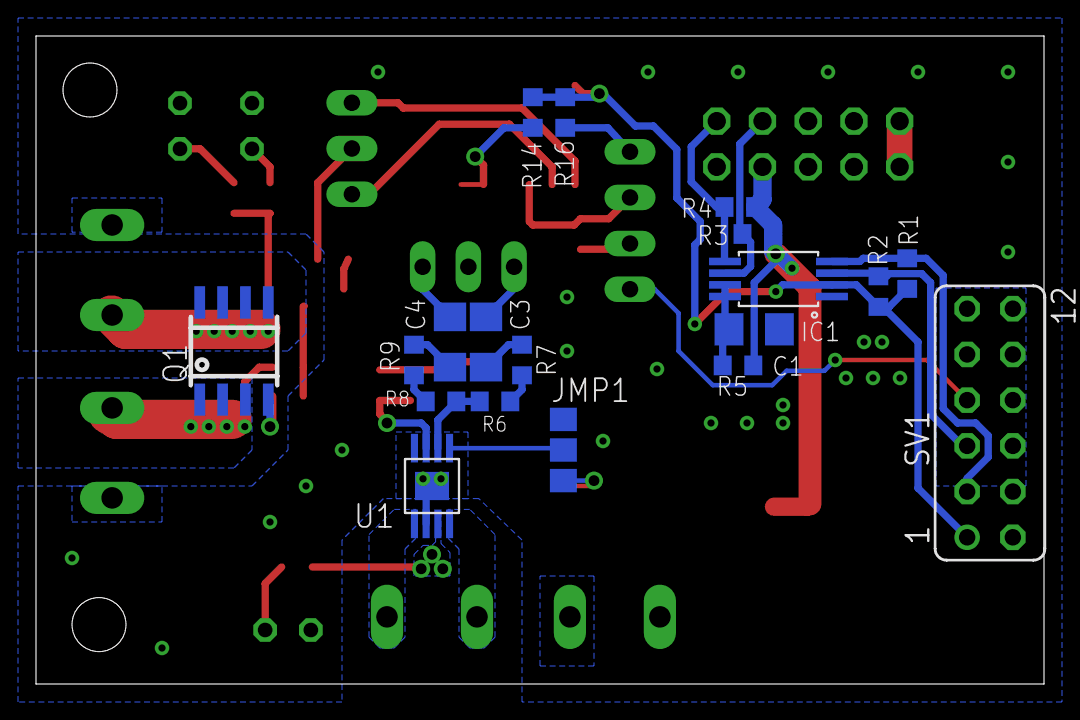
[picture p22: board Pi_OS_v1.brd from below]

Board: 2 copper layers, 56.0 x 36.0 mm, 53 parts (19 on the bottom side), 38 nets.

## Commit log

2020-06-01 Initial commit.
    [base.obj, base_A.obj, base_O.obj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]
2022-10-26 Updating BOM
2022-10-26 Adding PCB files
    [Pi_OS_v1.brd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]

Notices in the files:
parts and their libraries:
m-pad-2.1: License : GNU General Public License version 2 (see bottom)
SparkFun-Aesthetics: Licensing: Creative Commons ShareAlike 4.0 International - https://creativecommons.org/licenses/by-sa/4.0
